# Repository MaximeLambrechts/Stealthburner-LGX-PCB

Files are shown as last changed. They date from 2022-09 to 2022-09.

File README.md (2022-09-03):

# PCB for Voron Stealthburner & Bondtech LGX

This mod is a custom 2-piece PCB design, as well as a few printed parts, to make the Bondtech LGX fully compatible with the Voron Stealthburner.

This mod is based on two existing mods, all credits go to them for the initial design :

* LGX Stealthburner Mount Remix by Symataris on Thingiverse ([link here](https://www.thingiverse.com/thing:5242645))
* Stealthburner toolhead PCB by Hartk1213 ([link here](https://github.com/hartk1213/MISC/tree/main/PCBs/Stealthburner_Toolhead_PCB))

I really like the 2-piece PCB design by Hartk, with which you just plug the stealthburner in the main board via a connector, without having to deal with cables from the fans and LEDs.

Instead of trying to source different parts from different mods and make them all compatible with each other, I decided to create this mod and design 2 new PCB's (one for the stealthburner, one on the LGX), as well as the printed parts required to have a fully completed Stealthburner + LGX, as cleanly assembled as possible.

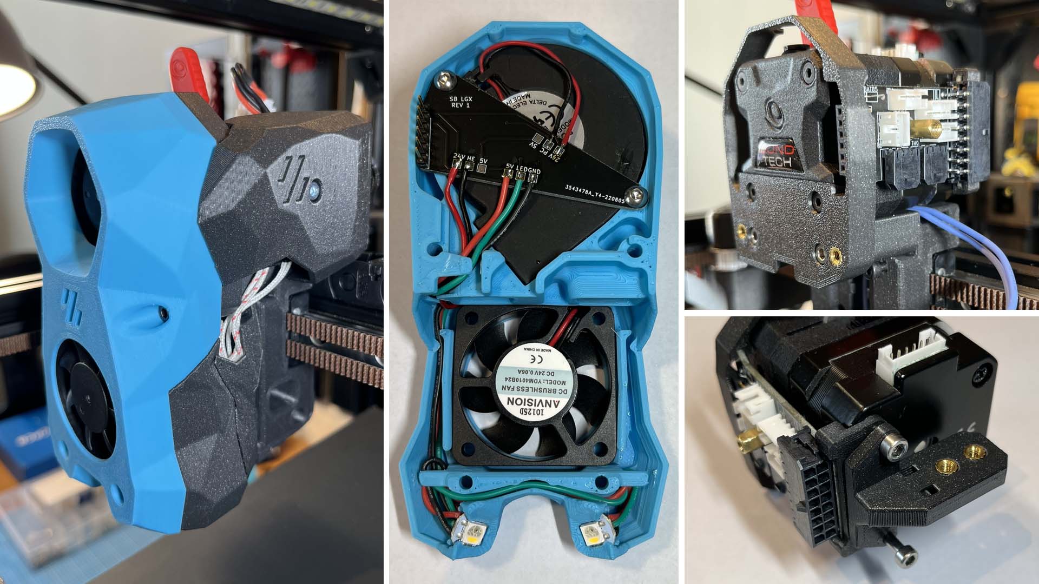
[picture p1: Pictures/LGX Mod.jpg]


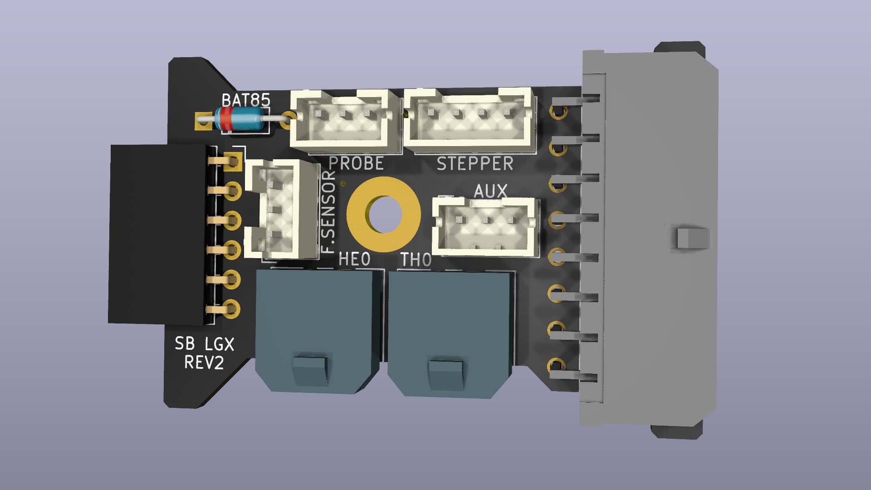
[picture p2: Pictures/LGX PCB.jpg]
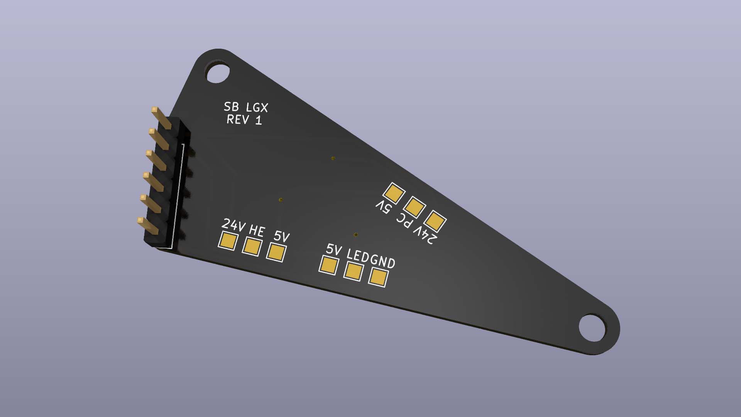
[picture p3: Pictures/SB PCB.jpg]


[1. Bill of Materials (BOM)](#1-bill-of-materials)

[2. Ordering PCBs](#2-ordering-pcbs)

[3. Printed parts](#3-printed-parts)

[4. Assembly Instructions](#4-assembly-instructions)

[5. Feedback](#5-feedback)

# 1. Bill of Materials (BOM)

Note: This BOM complements the original Stealthburner BOM. Only the extra compoments are included here. Items that are required for the original build are not included here. Refer to the stealthburner manual for a complete list of required components.

PCBs

* 1x Stealthburner side PCB (SB_PCB)
* 1x LGX side PCB (LGX_PCB)

Hardware

* 3x M3x6 Button head hex socket screws
* 1x 10mm standoff (female-female)
* 5x Heat set inserts (or 4 if using 2-hole cable chain)
* 1x M3x6 Socket head Cap Screws
* 2x M3x18 Socket head Cap Screws
* 2x M3x20 Socket head Cap Screws
* 2x M3x25 Socket head Cap Screws
* 2x M3x30 Socket head Cap Screws
* 2x M3x8 Flat head Screws (can be slightly longer, not critical)

Connectors & Electronics

* 1x Pin header, 6 pos, 2.54mm (Molex 22-28-4063)
* 1x Pin Socket, 6 pos, right angle through hole (Samtec SSW-106-02-G-S-RA)
* 1x Molex 43045-1600 (Board 16-pin receptacle)
* 1x Molex 43025-1600 (16-pin connector)
* 16x Molex 43030-0007 (contacts for wires)
* 2x Molex 43650-0200 (Hotend & Thermistor receptacles)
* 2x Molex 43645-0200 (Hotend & Thermistor connectors)
* 1x BAT85 diode (optional, if using probe only)
* 3x JST-PH 3-pin male & female
* 1x JST-PH 4-pin male & female

(Note: JST-PH connectors can be bought in assortment boxes on Amazon for example. I recommend this, as you would have multiple sizes in male/female in sufficient quantity for this and future projects, or should you need to recrimp a new cable for example)

Other

* 1x Small PTFE tube (2mm ID x 4mm OD) (length varies depending on your hotend. See assembly instructions).
* Small zipties

# 2. Ordering PCBs

Two Gerber zip files are provided for ordering the PCB's (**LGX_PCB_Gerber.zip** and **SB_PCB_Gerber.zip**).

I recommend JLCPCB or PCBWay for ordering the PCBs. I've personally ordered from JLCPCB and the boards were very cheap and worked perfectly.

An example order configuration for JLCPCB can be found [here](Pictures/PCB%20Order/JLCPCB.jpg).

An example order configuration for PCBWay can be found [here](Pictures/PCB%20Order/PCBWay.jpg).

Pay attention to the important settings (marked with an exclamation point) when ordering the PCB's!

The LGX PCB should be a **4-layer board of 1.6mm thickness**. (on JLCPCB only, you have to specify which layer is which, see picture)

The SB PCB should be a **2-layer board of 1.6mm thickness**.

Other parameters are personal preference, like the color of the board, or if you want lead-free HASL for example.

# 3. Printed parts

The following parts need to be (re)printed :

* **Stealthburner_Body.stl** (There are small differences to the original file. Some small cutouts for a better PCB fit and the PCB mounting
points have been modified.)
* **LGX_Mount.stl**
* **LGX_Rear_PCB_Support.stl**
* **Cover.stl**
* **Cable_Chain_Anchor_xHoles..stl** (Chose either the 2 or 3-hole version depending on your cable chain)

# 4. Assembly Instructions

Note: These instructions are a complement to the original Stealthburner assembly manual. Keep a copy of the original manual open in parallel 
to these instructions, as I will often refer to it.

## Preparing the PCBs

* Solder the components on the LGX pcb as shown on the picture. Make sure the 6-pin socket lays nice and flat on the PCB and is soldered straight. This is important for correct connection with the stealthburner later on.

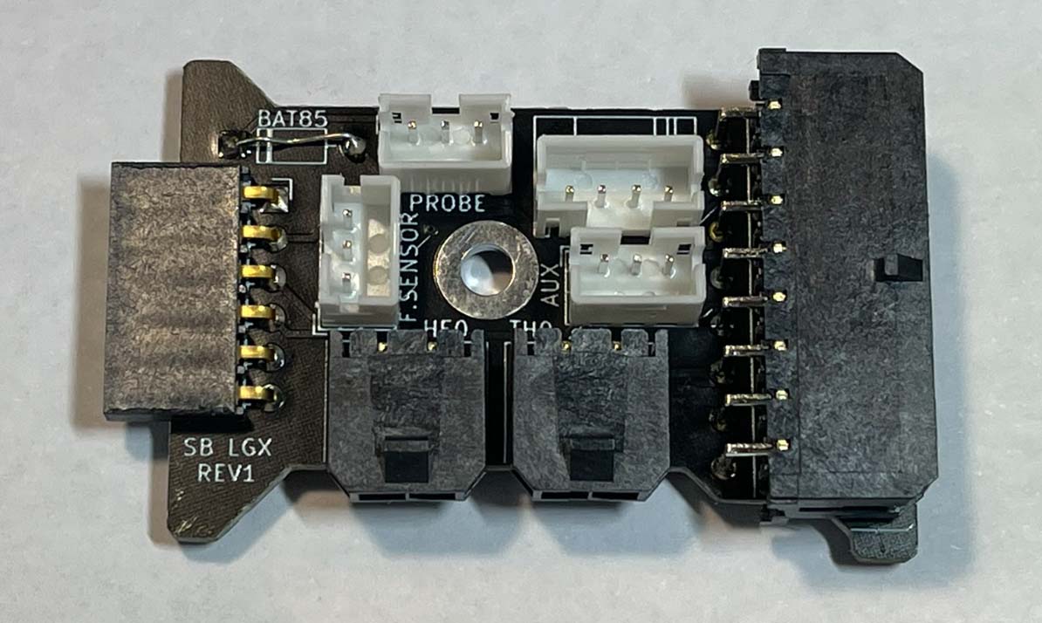
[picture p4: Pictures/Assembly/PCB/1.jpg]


* If you're not using an inductive probe (for example Klicky or KlickyNG mod with microswitch), replace the BAT85 diode by a small piece
of wire to short the pads. A leg from a donor component (LED or resistor for example) works well here.

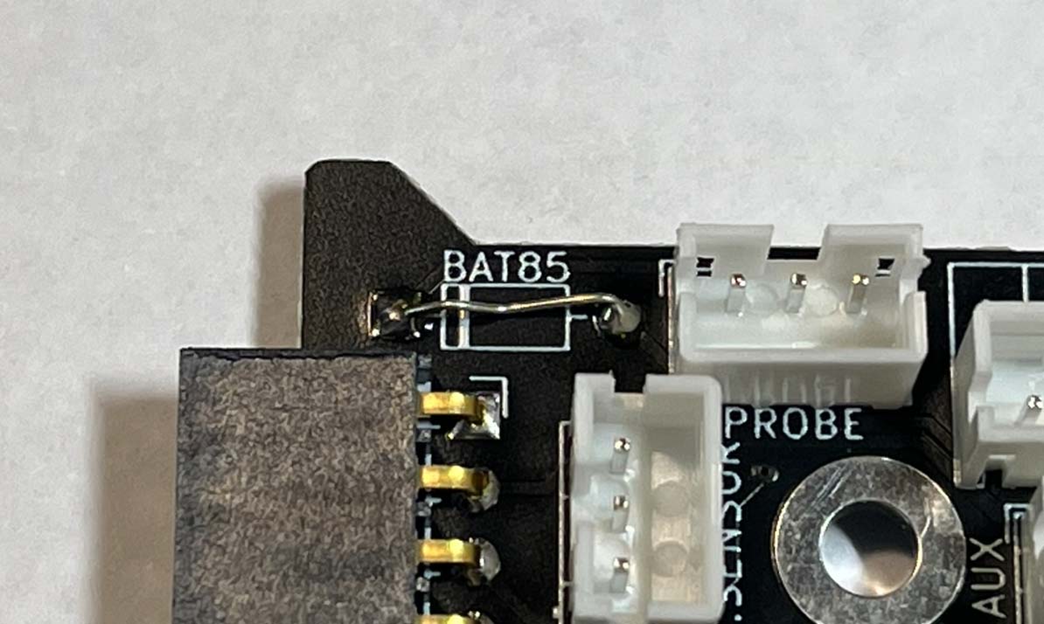
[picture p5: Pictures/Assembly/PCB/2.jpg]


* Install a 10mm standoff using an M3x6 button head screw.
Make sure the screw head **does not stick out more than 2mm from the PCB**.
Make sure **no solder points stick out more than 2mm**. (to avoid touching and potentially shorting on the LGX extruder motor later on)

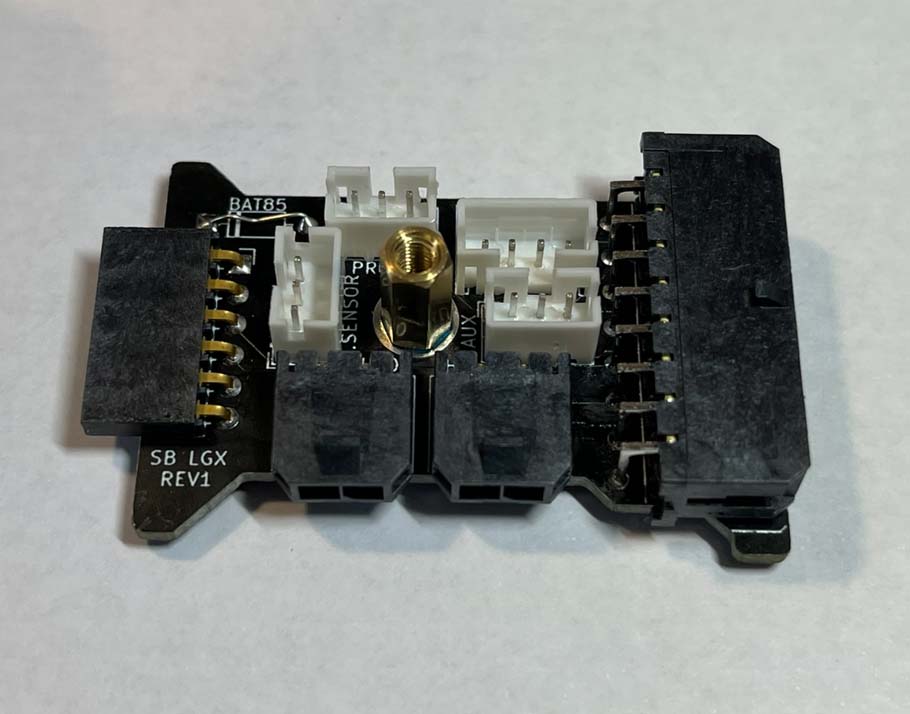
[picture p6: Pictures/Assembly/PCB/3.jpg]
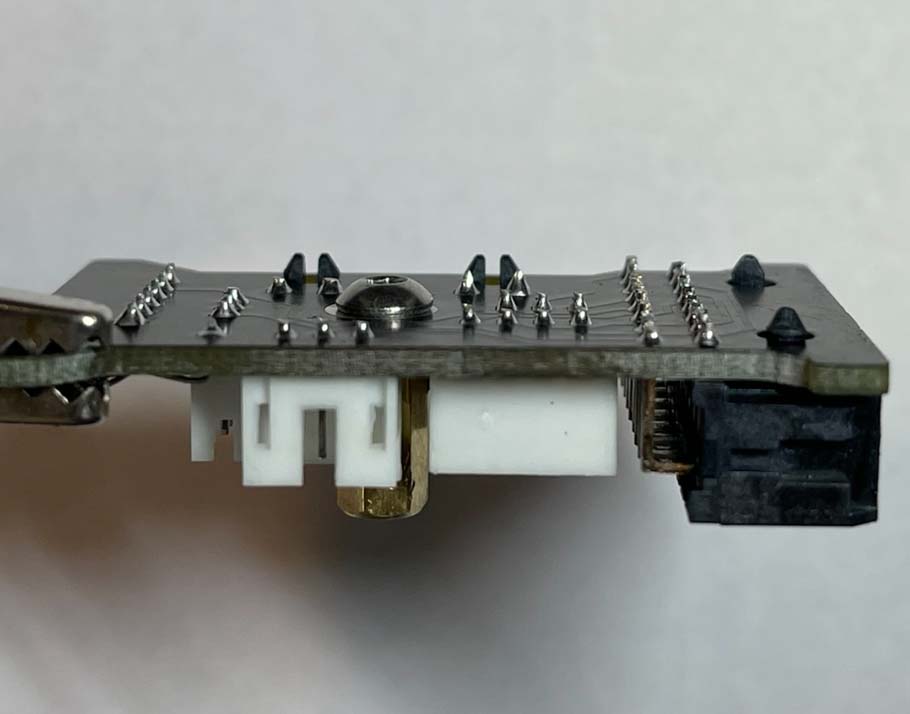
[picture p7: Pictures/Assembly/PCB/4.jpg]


* Solder a 6-pin header to the SB PCB. The pins should face up.

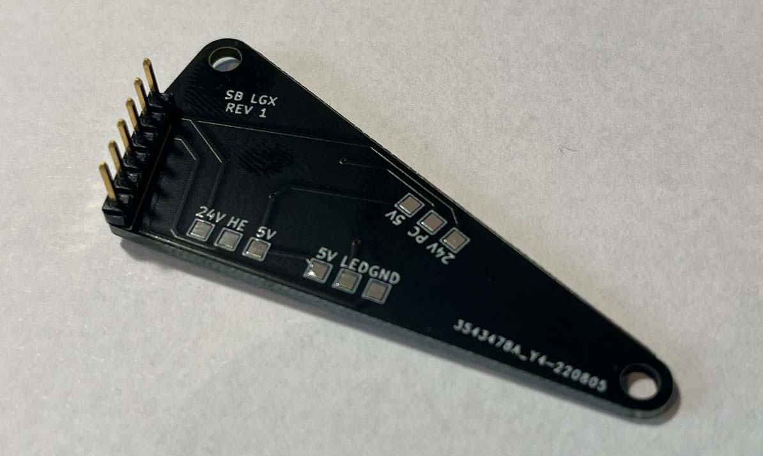
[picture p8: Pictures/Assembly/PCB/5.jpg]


## Stealthburner

* Follow the original manual instructions to install the LED's and fans into the stealthburner body. Leave the cables hanging for now.

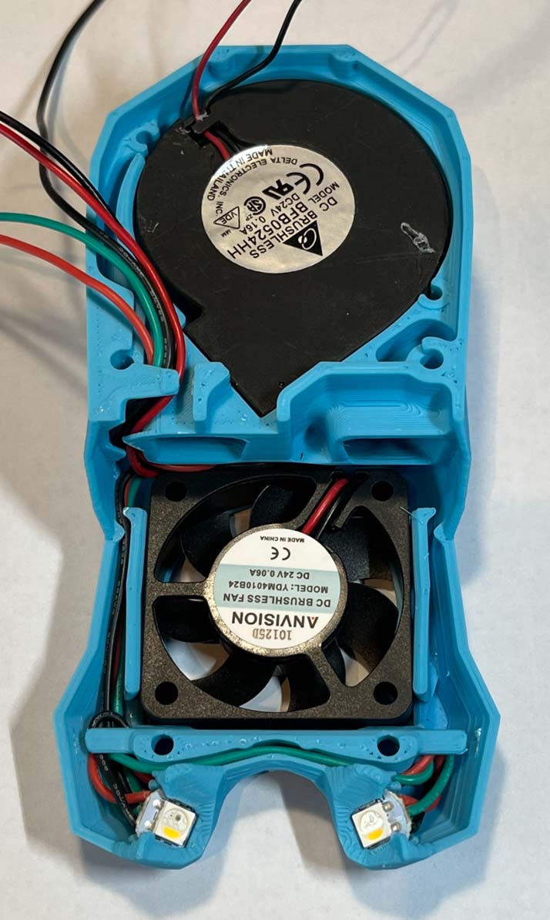
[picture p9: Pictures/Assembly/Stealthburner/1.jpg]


* Install the PCB into the SB body and fasten with 2 M3x6 button head screws.
**Warning**: Do not overtighten as these screw into plastic.

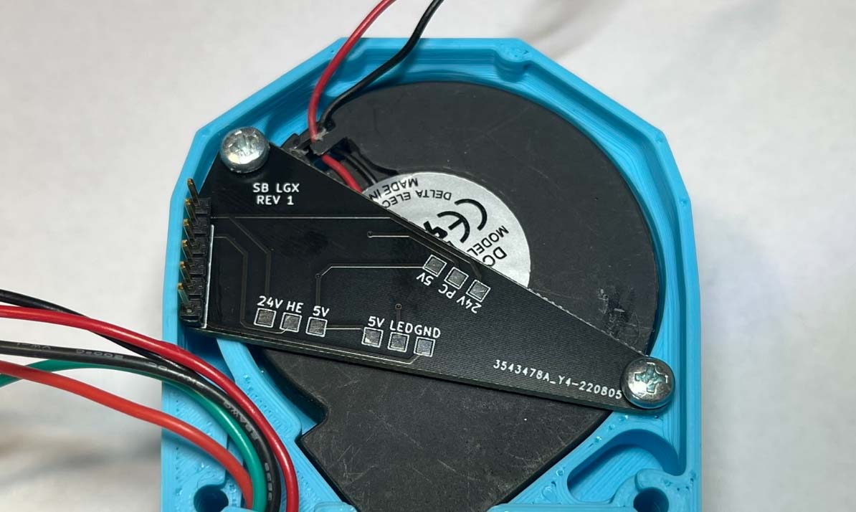
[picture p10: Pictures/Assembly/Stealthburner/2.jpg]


* Make sure the screws do not stick out of the SB body, or there would be a clearance issue with the LGX. (That's the reason why button head screws are used here instead of socket head)

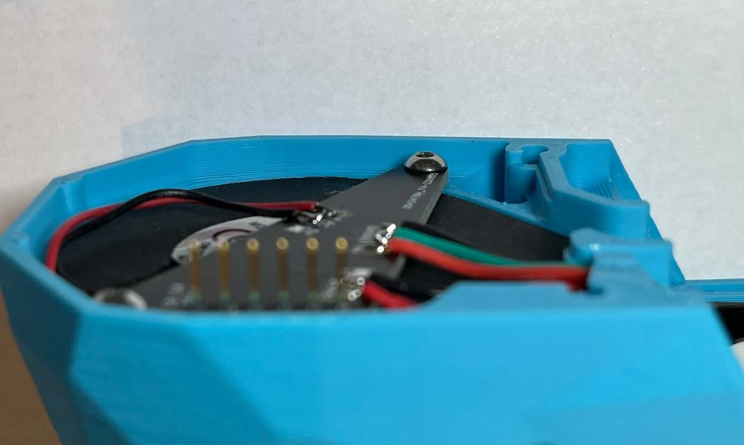
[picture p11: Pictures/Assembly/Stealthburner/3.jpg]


* Solder all the wires onto the PCB as shown on the picture below. Note: The red (positive) wire of both fans can be soldered to either 24V or 5V 
depending on the voltage of your fans.

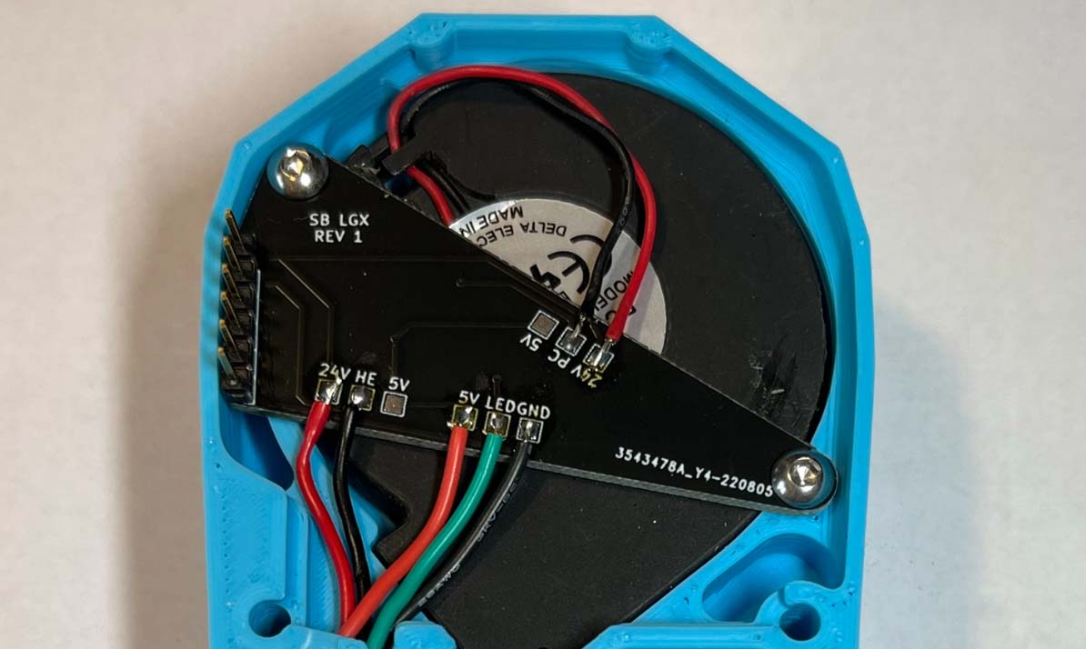
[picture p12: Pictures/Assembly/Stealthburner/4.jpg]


## Printhead

* Follow the stealthburner manual to assemble the printhead. You can print either the CW1 or CW2 version of the printed parts.

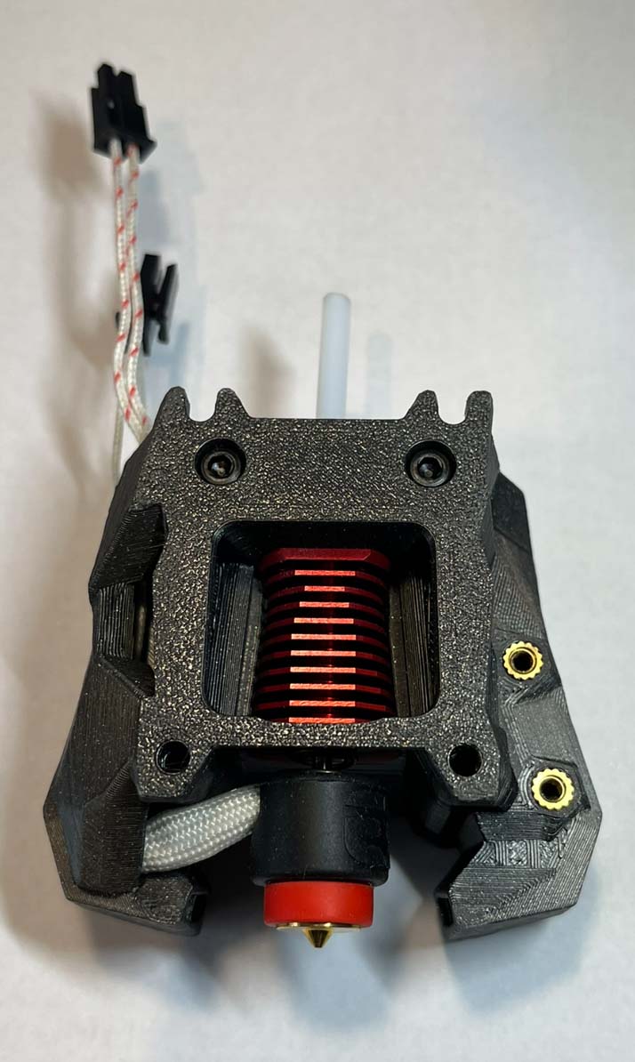
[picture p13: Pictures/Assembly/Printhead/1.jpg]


* Install the PTFE tube into the hotend. The length of the tube will vary depending on your hotend. The tube should stick out **25mm** from the top of the printed part.

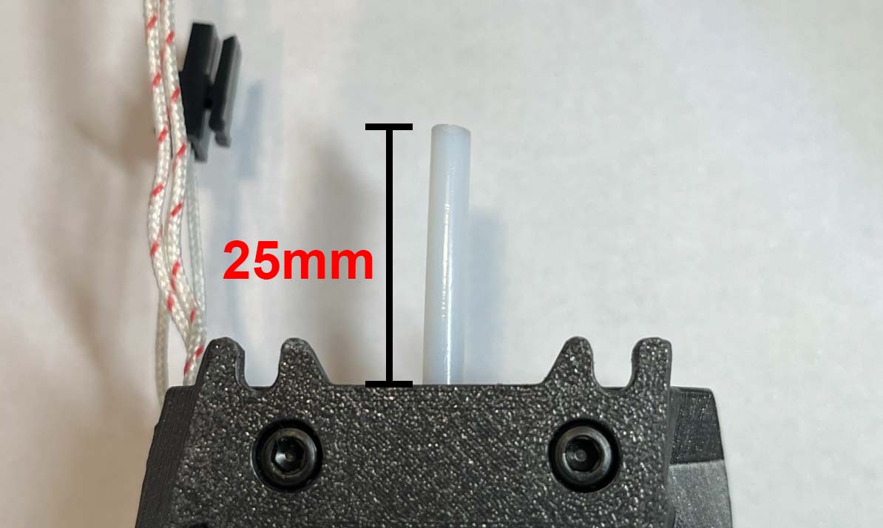
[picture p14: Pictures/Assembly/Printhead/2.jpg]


## LGX

* Install 2 heat set inserts into the LGX Mount as shown. 
Install 2 (or 3) heat set inserts into the cable chain anchor as shown.

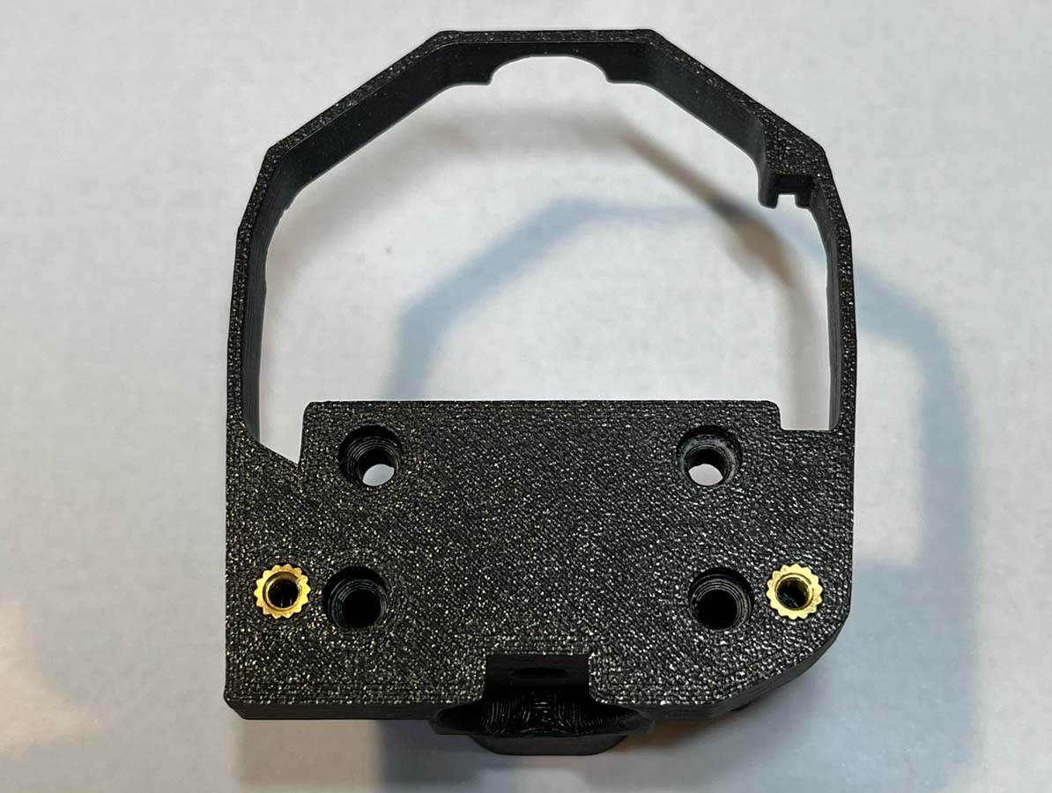
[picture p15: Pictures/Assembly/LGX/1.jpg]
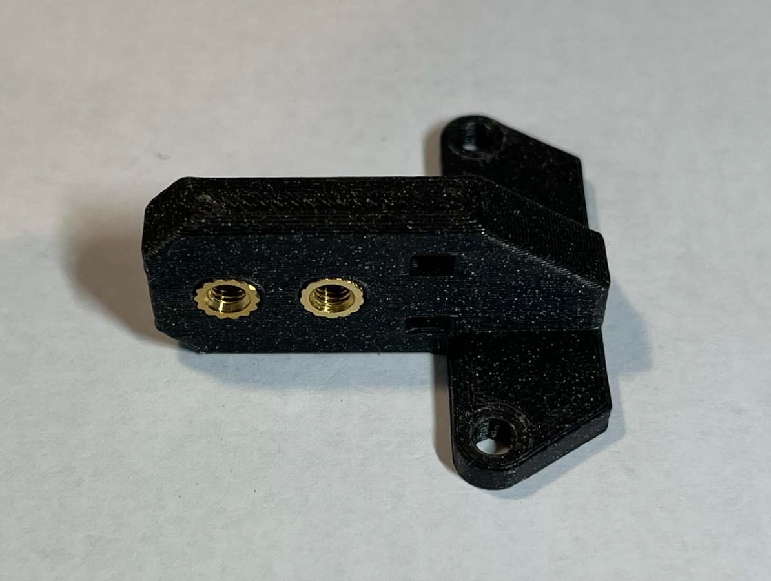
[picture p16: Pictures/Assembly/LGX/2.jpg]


* dissasemble the front part of your LGX extruder.

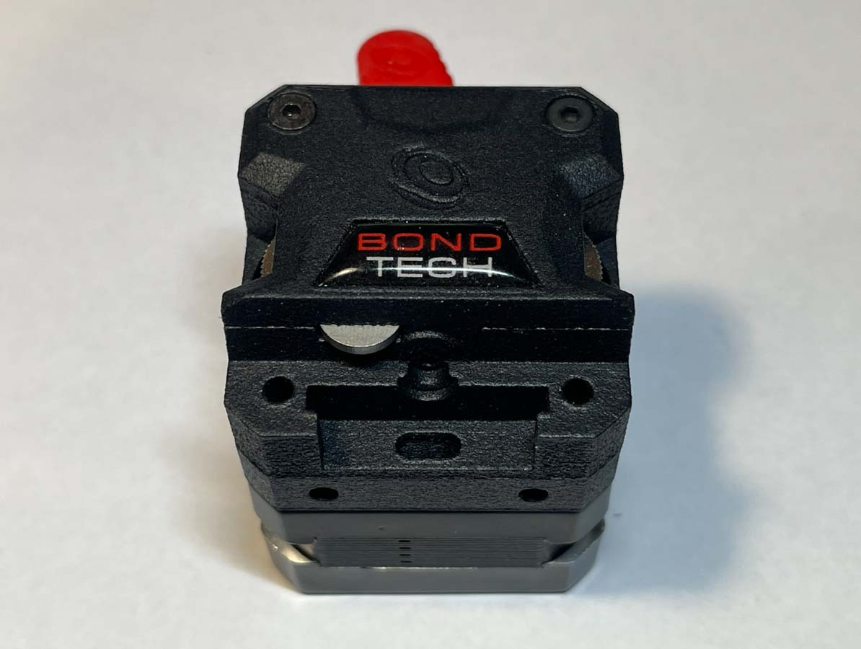
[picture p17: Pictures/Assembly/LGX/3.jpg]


* On the backside, remove the 2 left screws.

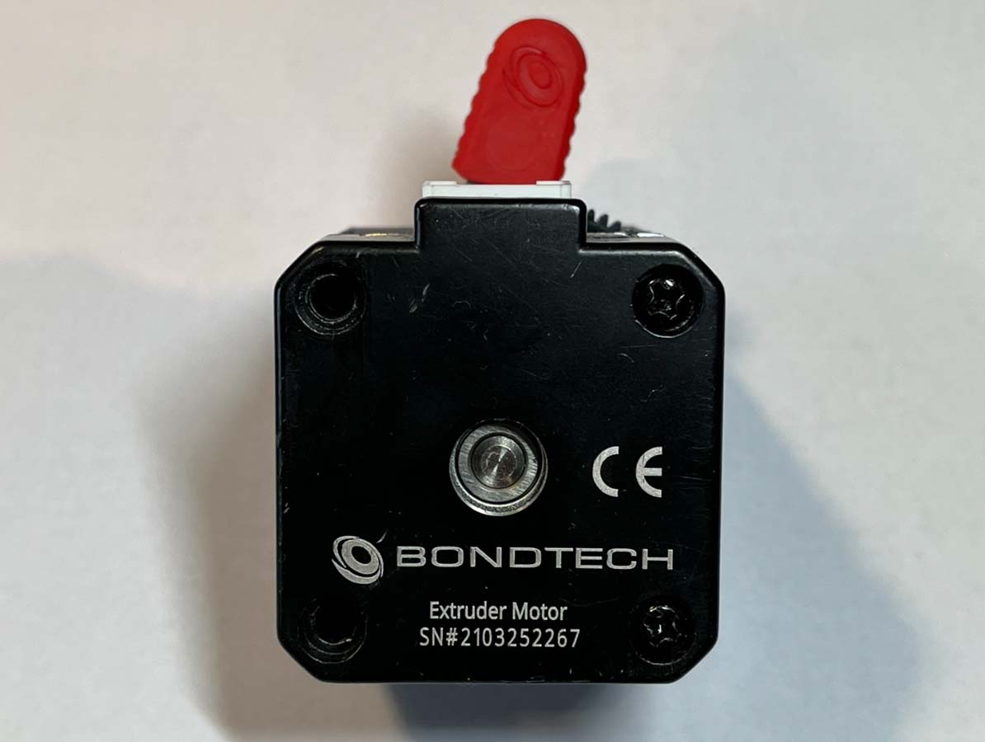
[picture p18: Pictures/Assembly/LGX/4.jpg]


* Slide the LGX_Mount onto the LGX extruder and fasten with 2 M3x20 on the bottom and two M3x27 (original screws from LGX) on the front.

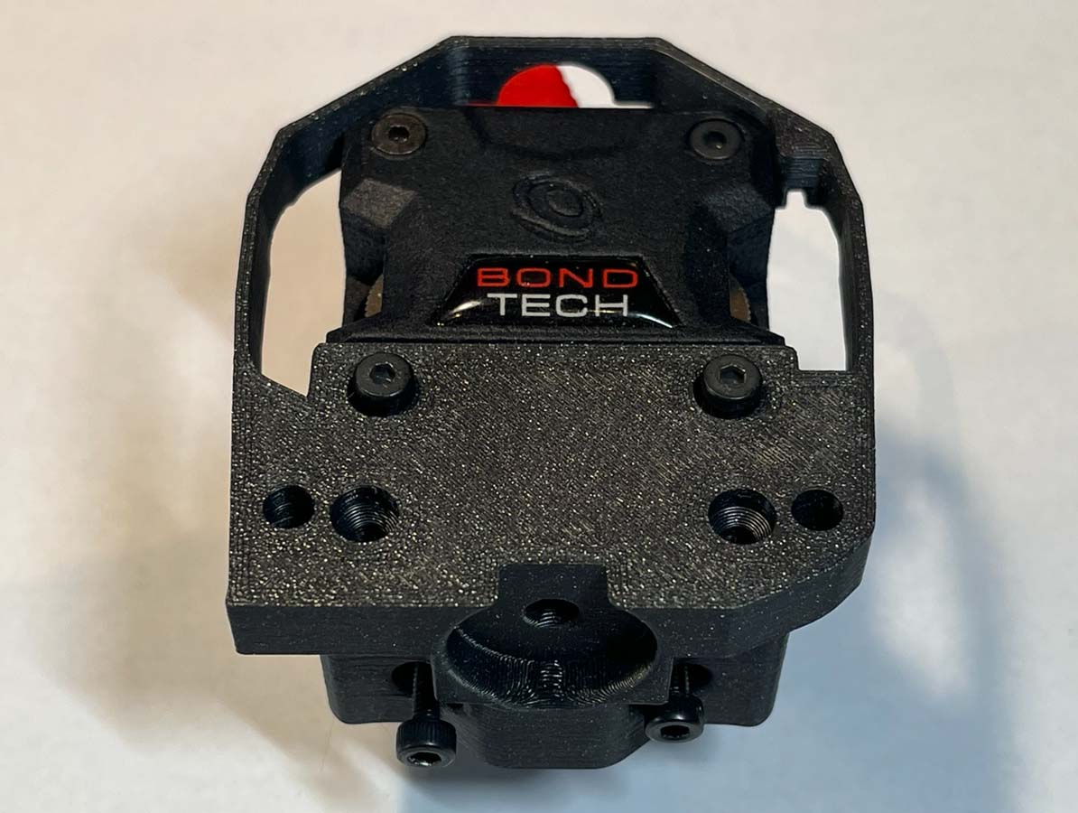
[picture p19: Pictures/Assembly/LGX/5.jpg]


* Slide the PCB into the LGX_Mount printed parts grooves until it is fully seated into place.

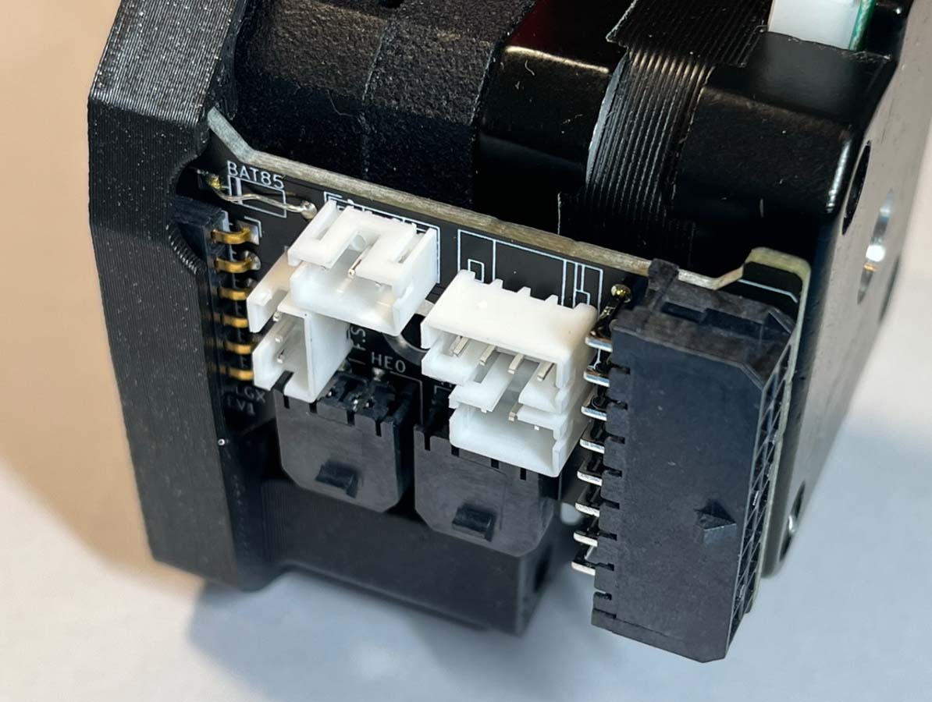
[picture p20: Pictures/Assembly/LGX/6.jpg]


* Install the PCB rear support printed part. It should slide onto the PCB and insert into the holes of the extruder motor.

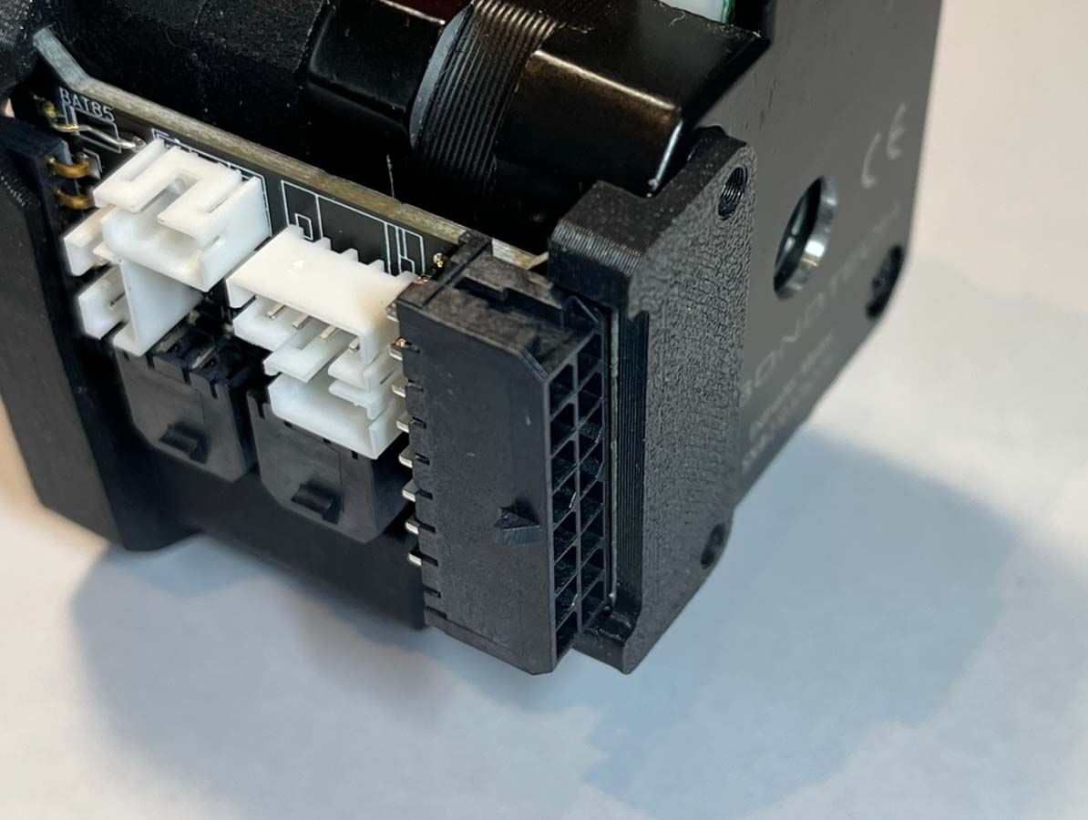
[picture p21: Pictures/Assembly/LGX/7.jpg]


* Install the cable chain anchor and fasten everything together with 2 M3x25 screws.

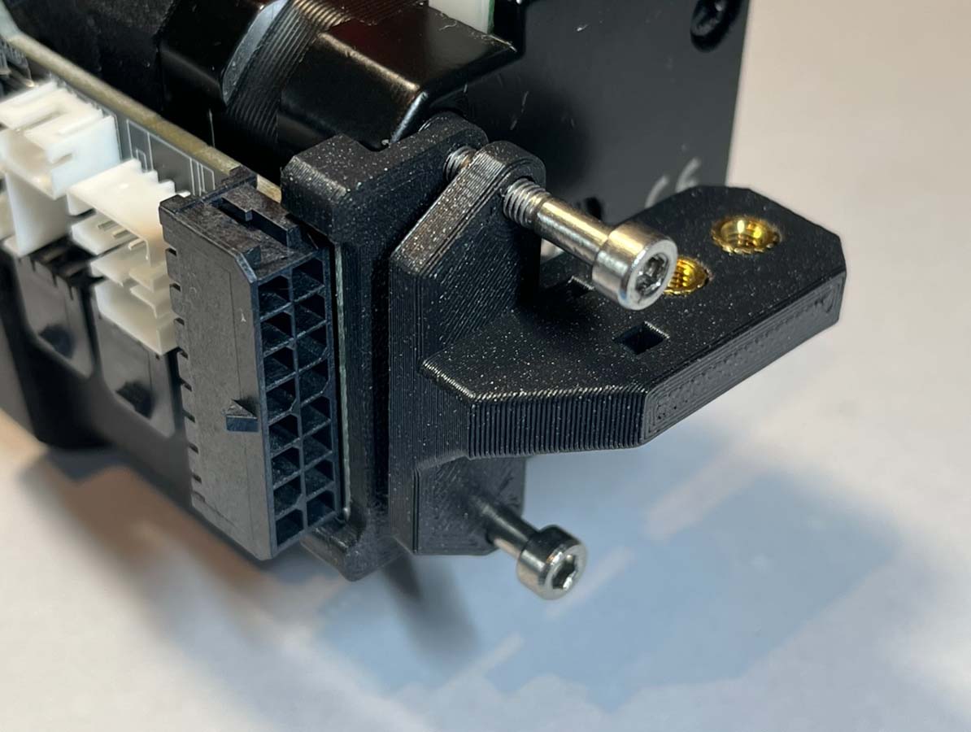
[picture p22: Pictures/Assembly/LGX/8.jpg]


* Now is a good time to make sure no solder points touch the LGX extruder motor.

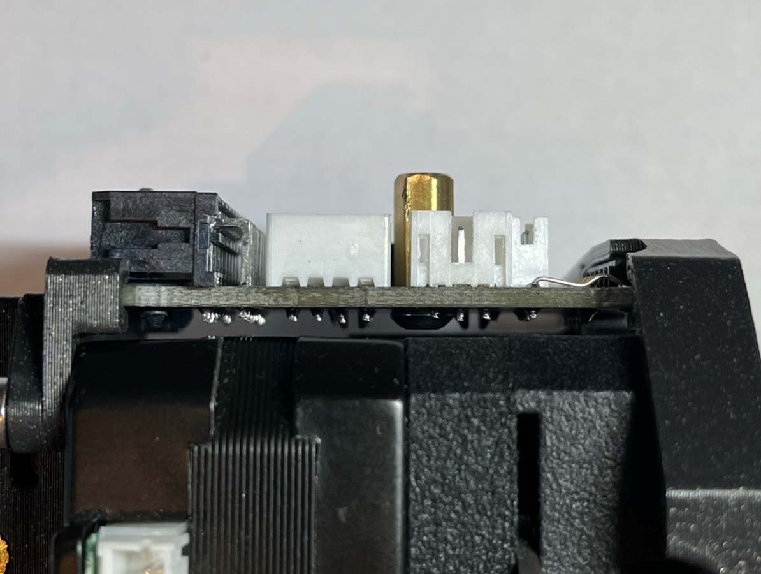
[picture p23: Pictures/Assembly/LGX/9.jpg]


## Final Assembly

* Follow the stealthburner manual to install the carriage and probe (or klicky).

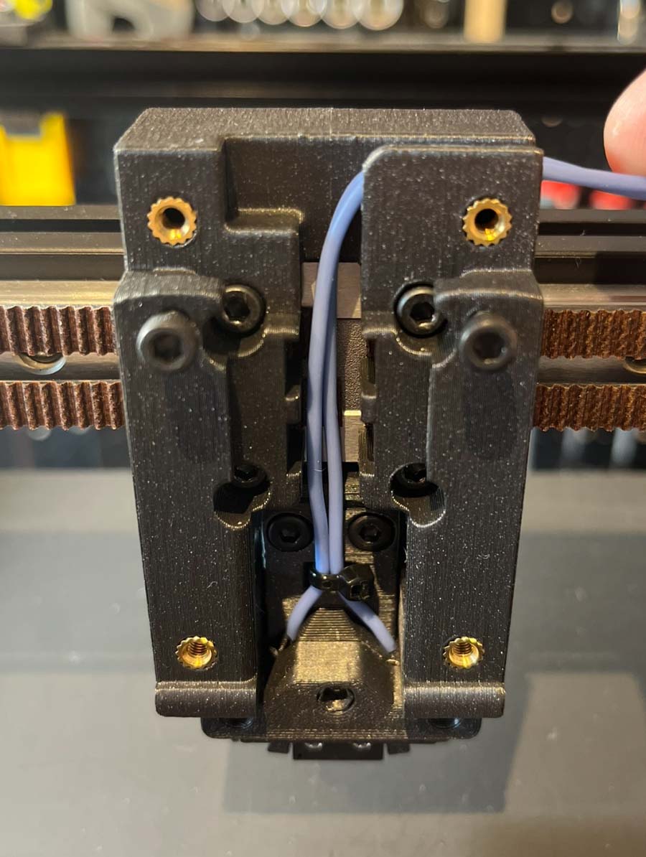
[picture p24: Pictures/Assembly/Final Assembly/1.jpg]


* Fasten the LGX assembly onto the carriage with 2 M3x30 screws.
Make sure the probe wires are routed correctly and are not pinched between the carriage and LGX.

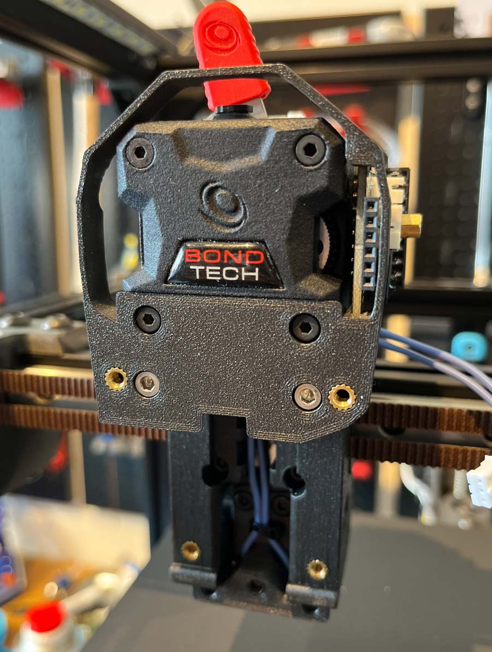
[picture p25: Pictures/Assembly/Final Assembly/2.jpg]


* Slide the printhead from the bottom into the LGX assembly. Make sure it is fully inserted, flush with the LGX mount, and flush on the X-carriage.

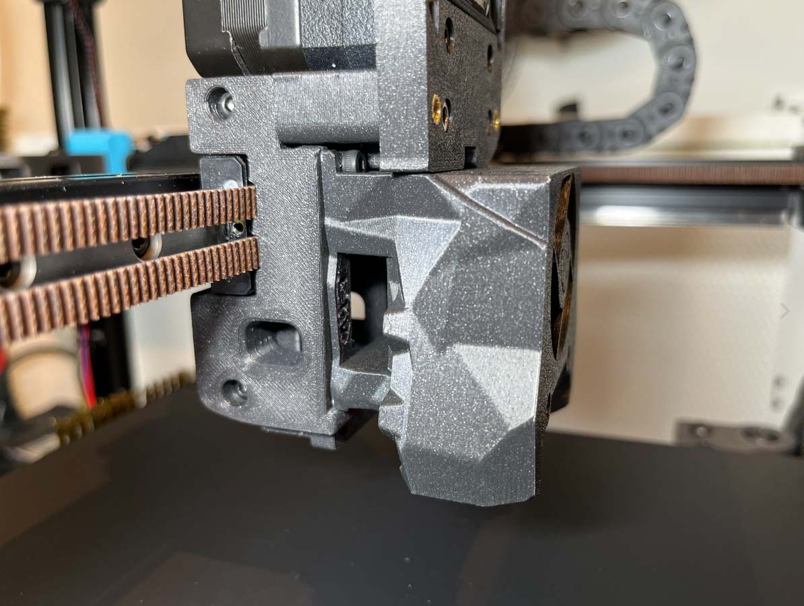
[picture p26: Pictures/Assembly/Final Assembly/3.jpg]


* Slide the Stealthburner in place. Make sure the pins align correctly with the socket. It is recommended to first align and insert the pins, then slide the SB fully in place.

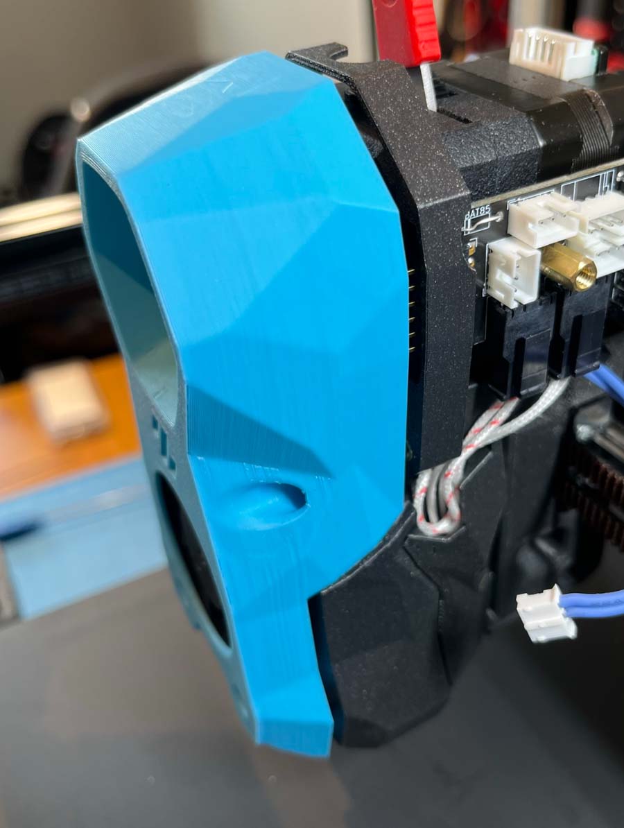
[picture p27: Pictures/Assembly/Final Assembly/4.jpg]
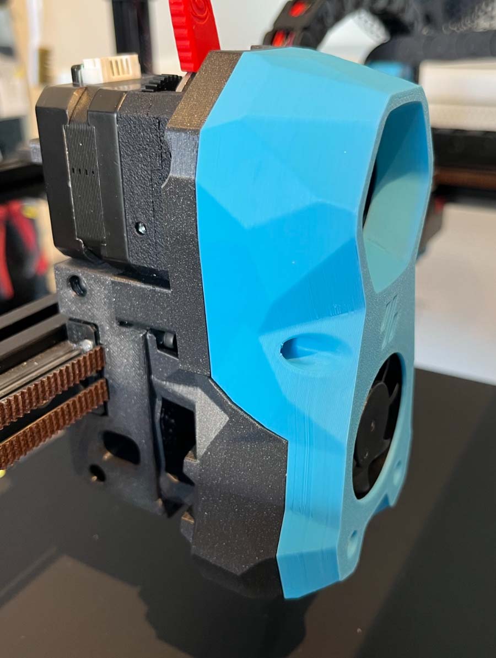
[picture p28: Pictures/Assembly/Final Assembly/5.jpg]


* Fasten the Stealthburner with 2 **M3x18** screws on top, and 2 **M3x50** screws on the bottom.

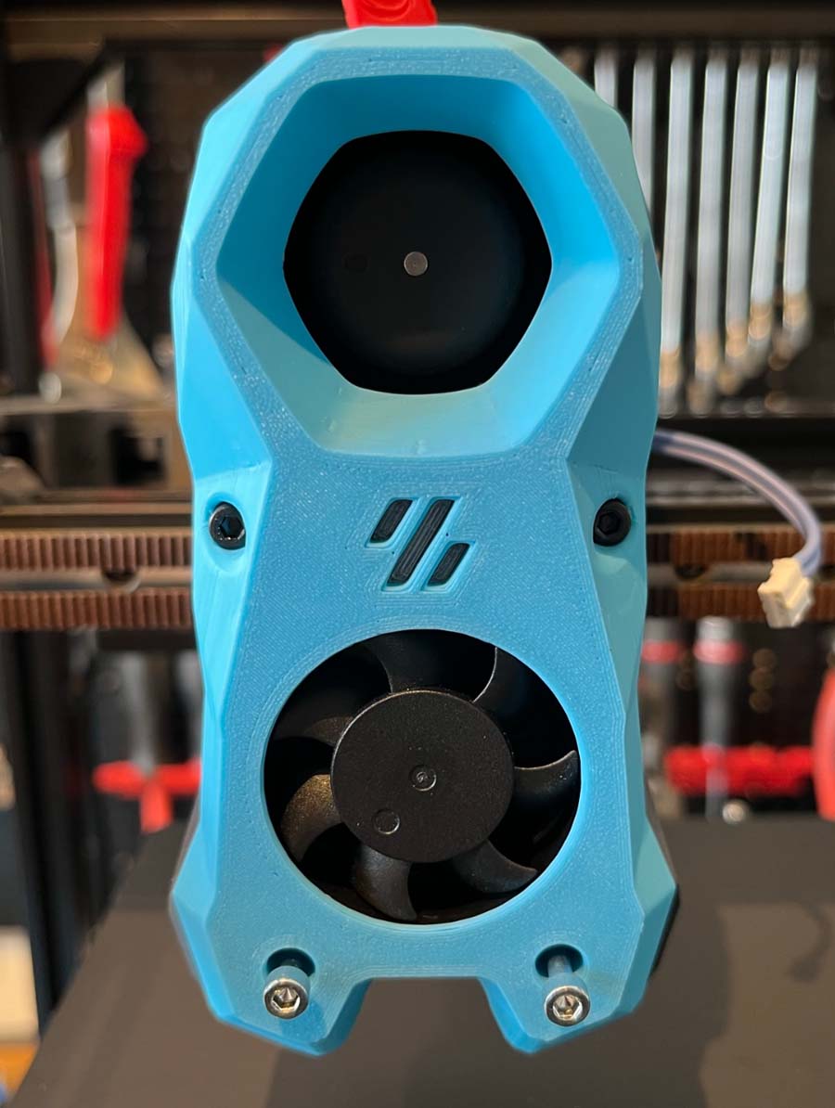
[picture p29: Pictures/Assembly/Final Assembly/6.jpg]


* Prepare a small cable for the extruder motor with JST-PH connectors as shown. Its length should be about **90mm**.

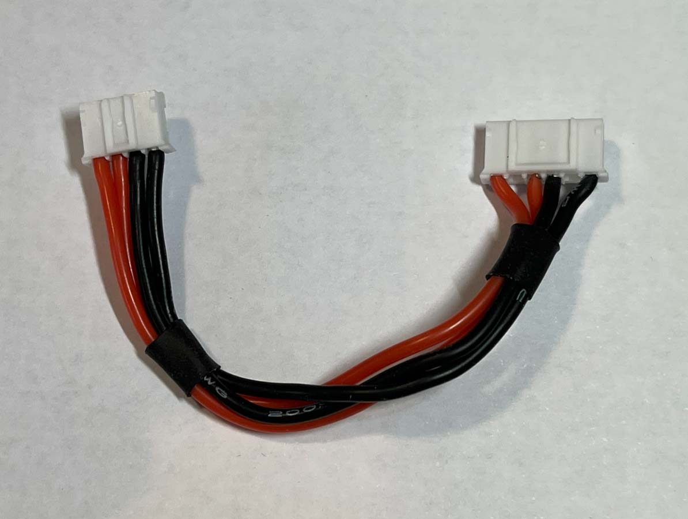
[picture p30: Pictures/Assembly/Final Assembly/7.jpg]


* Install the extruder motor cable.

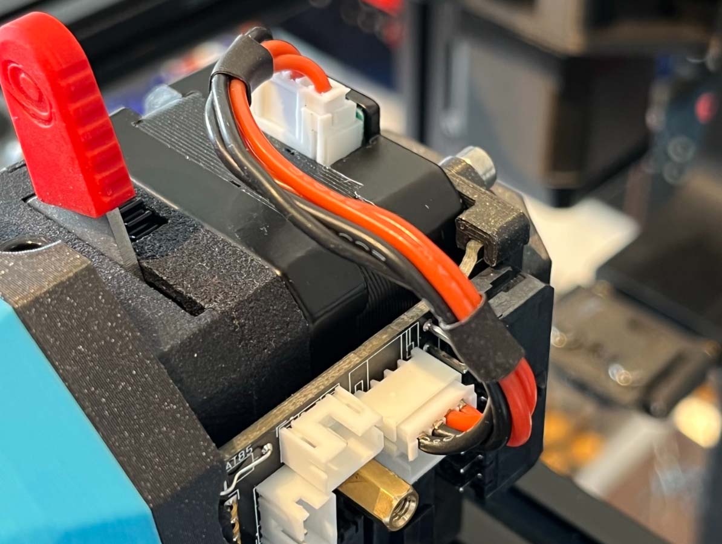
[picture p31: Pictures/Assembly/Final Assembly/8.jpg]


* Wire up the rest of the components, including the hotend, thermistor, probe or switch, etc

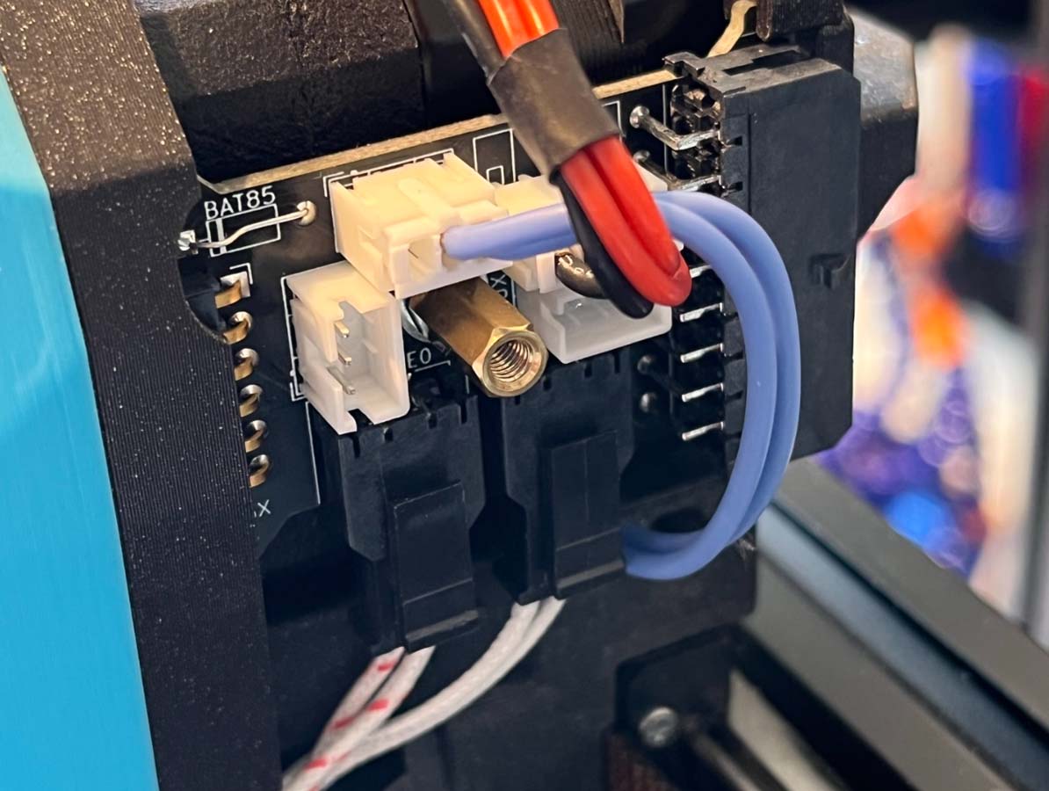
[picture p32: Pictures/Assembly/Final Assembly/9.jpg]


* Fasten the cable chain with 2 M3x8 flat head screws.
Install a ziptie into the ziptie slot.

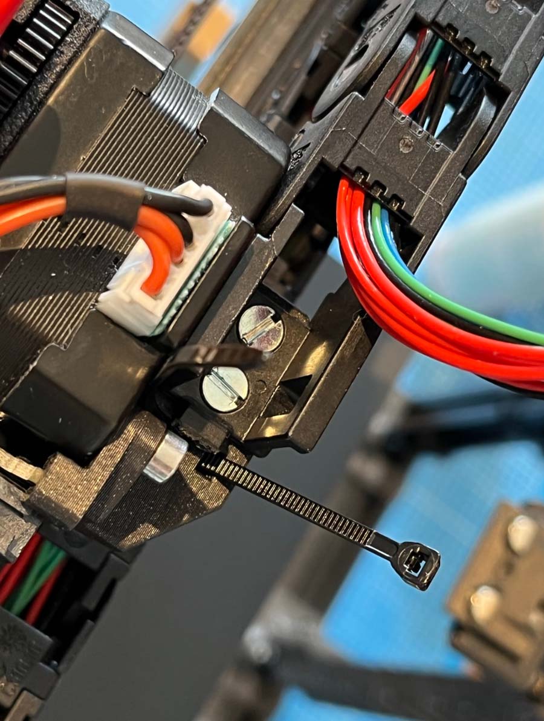
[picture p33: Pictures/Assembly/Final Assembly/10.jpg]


* Wire up and install the 16-pin connector. The wiring schematic is the same as the original Hartk PCB. The only difference is that the 14 and 2-pin connectors have been joined into a single 16-pin connector. The individual wires position is identical. See the wiring instructions [here](https://github.com/hartk1213/MISC/tree/main/PCBs/Stealthburner_Toolhead_PCB/Images/Wiring).

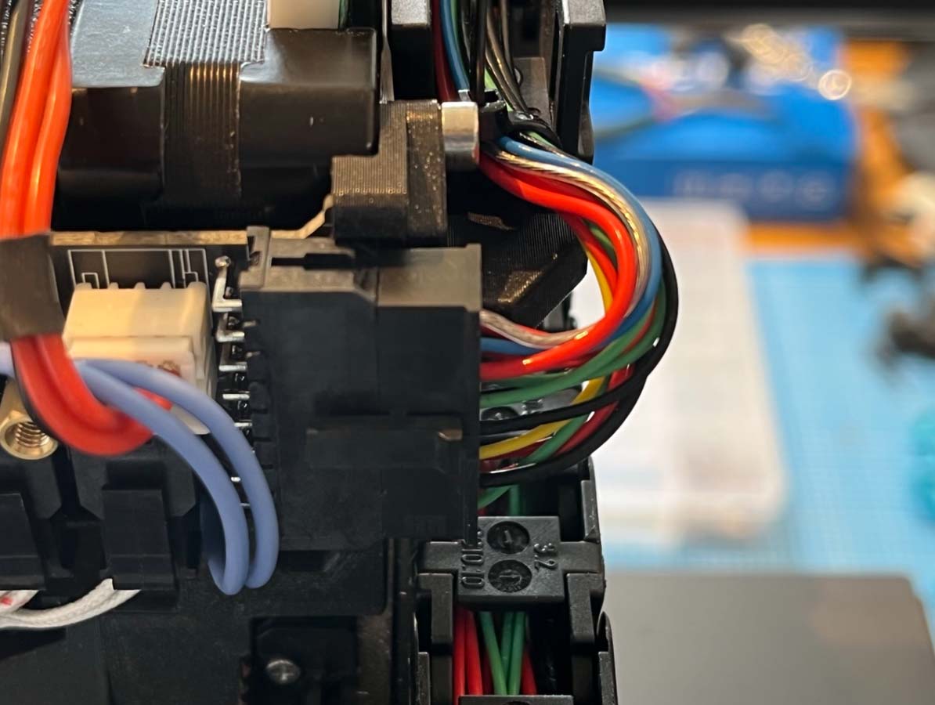
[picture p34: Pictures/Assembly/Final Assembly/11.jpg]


* Optionally, install a chamber thermistor. I've attached mine at the backside on the cable chain and routed the wires to the AUX connector on the PCB.

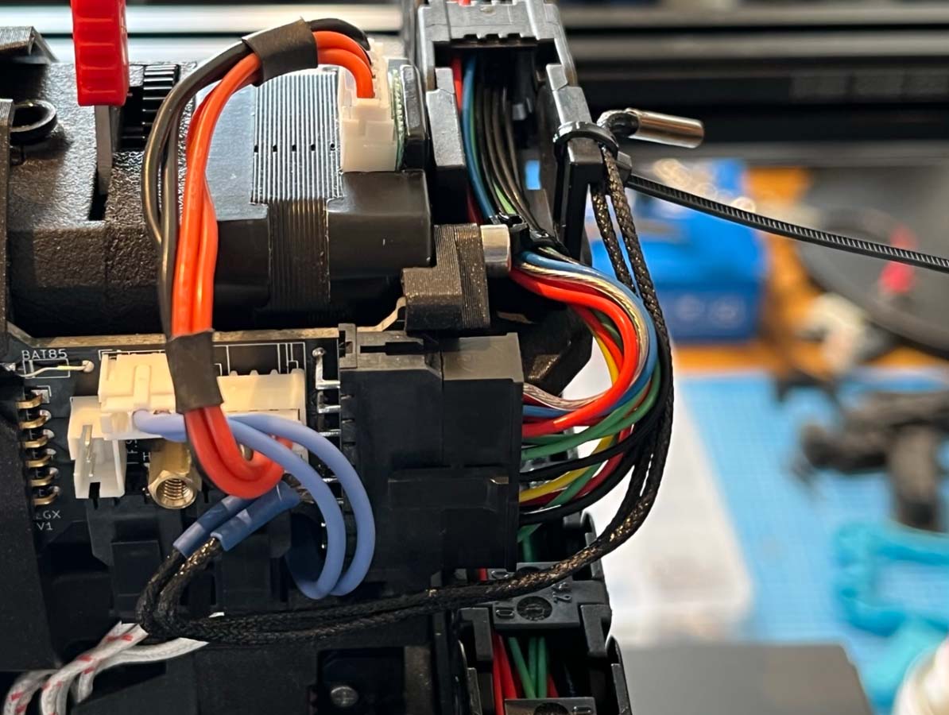
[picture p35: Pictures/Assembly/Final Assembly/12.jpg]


* Install the cover by sliding the backside over the M3 screws sticking out of the LGX, and then fasten on the side with 1 **M3x6** Socket head Screw.

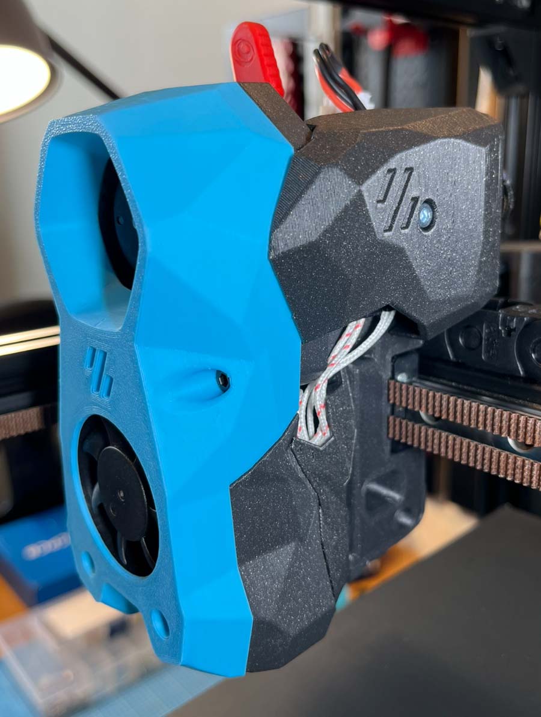
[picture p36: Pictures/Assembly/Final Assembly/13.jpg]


## Done ! Happy printing!

# 5. Feedback

While I've manage to assemble everything on my printer, there may be issues I haven't thought of, mistakes on this page, or issues that will only arise after many hours of printing.

**USE THIS MOD AT YOUR OWN RISK!**

I'd appreciate any kind of feedback, good or bad.

If you encounter issues, please open an issue on this github page.

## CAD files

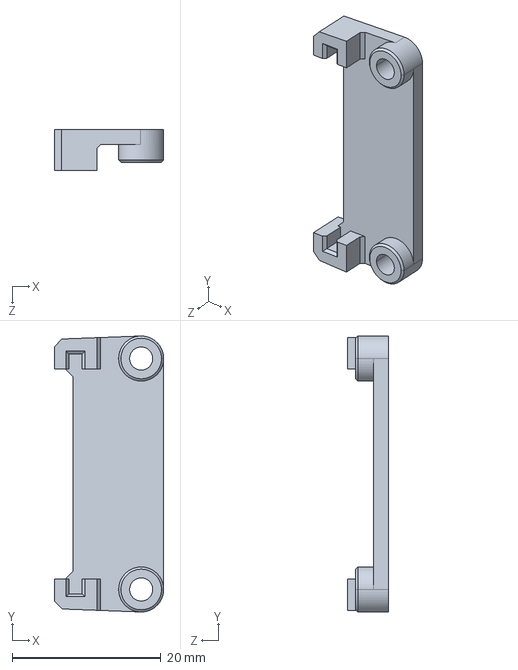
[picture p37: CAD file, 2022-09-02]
CAD/LGX_Rear_PCB_Support.STEP
14.7 x 37.1 x 5.50 mm

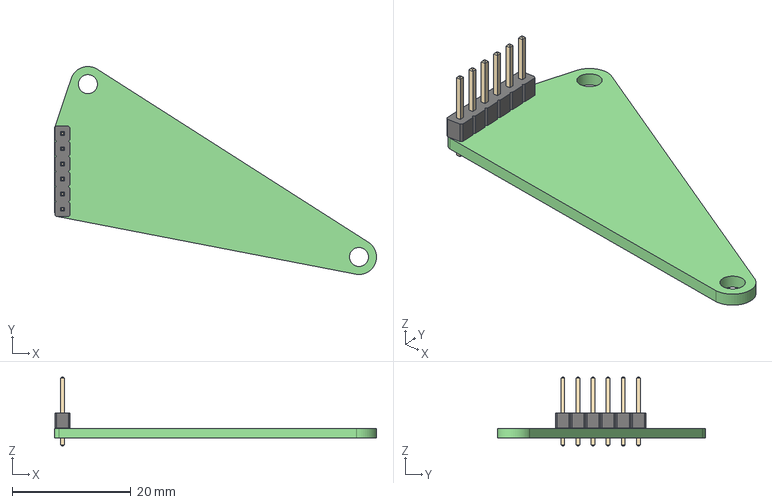
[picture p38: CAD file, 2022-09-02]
CAD/PCB/SB_PCB.step
54.1 x 35.0 x 11.5 mm
SB_PCB PCB

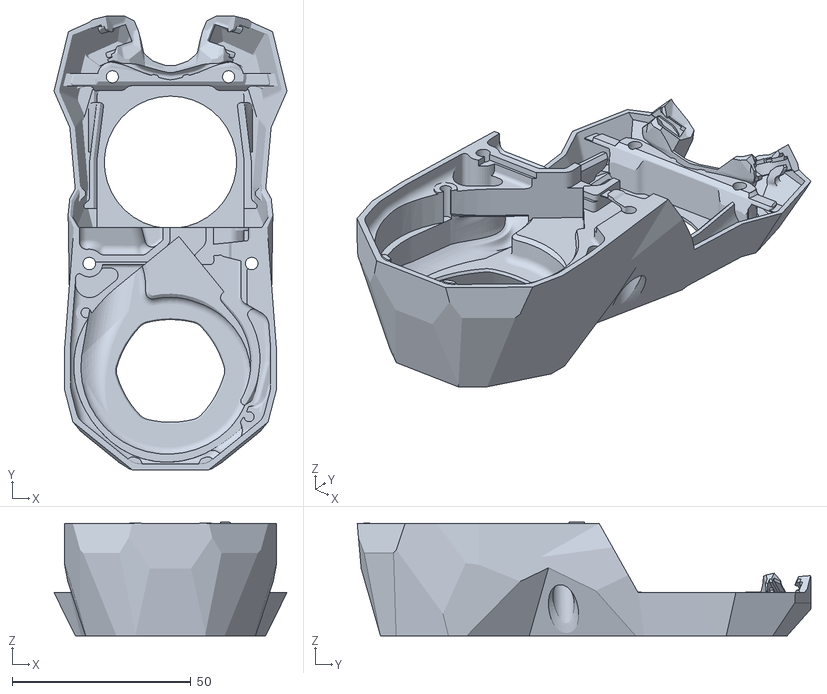
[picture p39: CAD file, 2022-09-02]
STL/Stealthburner_Body.STL
65.1 x 126.8 x 31.8

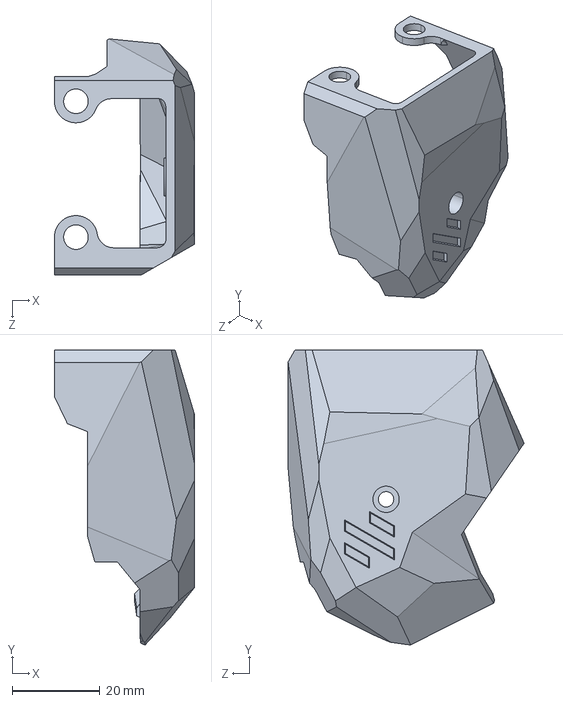
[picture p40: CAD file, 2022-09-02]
CAD/Cover.STEP
32.0 x 67.3 x 53.9 mm

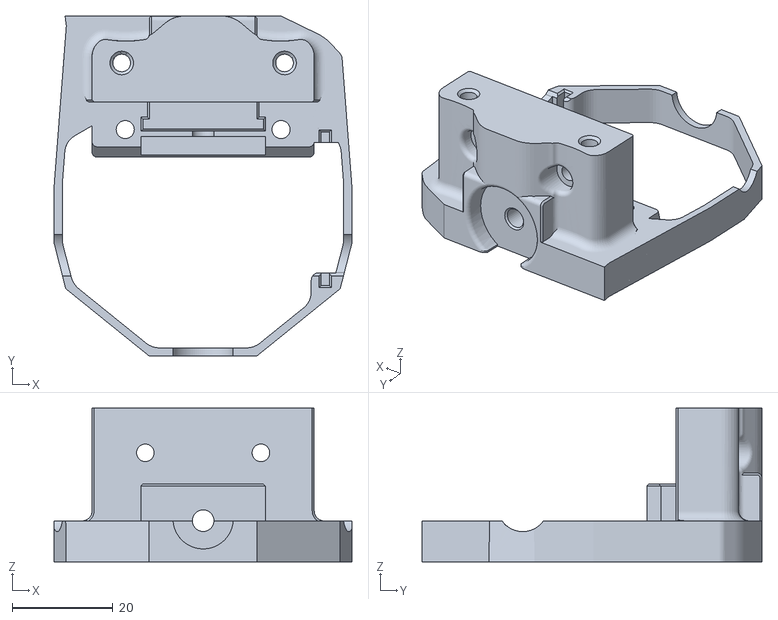
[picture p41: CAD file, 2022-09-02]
STL/LGX_Mount.STL
59.2 x 67.6 x 30.6

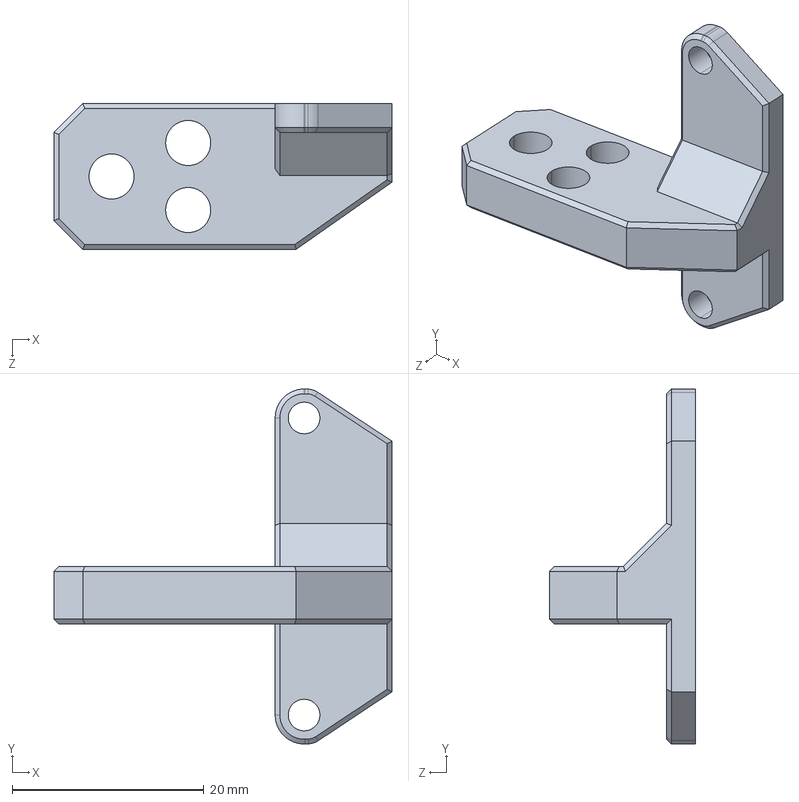
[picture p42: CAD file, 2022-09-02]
CAD/Cable_Chain_Anchor_3Holes.STEP
35.3 x 37.0 x 15.2 mm

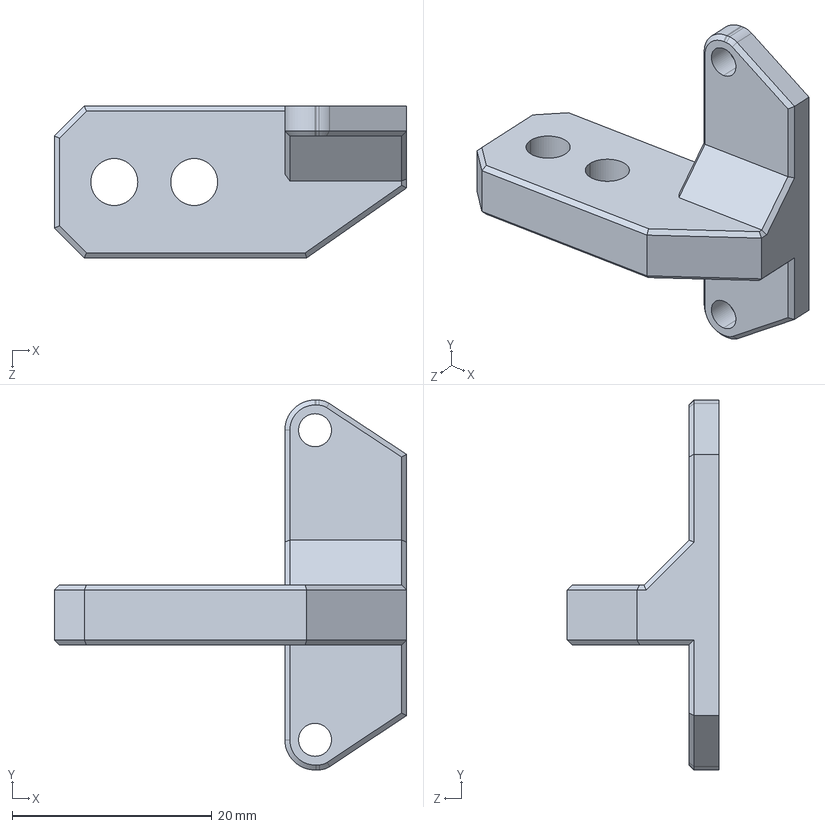
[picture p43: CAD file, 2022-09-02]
CAD/Cable_Chain_Anchor_2Holes.STEP
35.3 x 37.0 x 15.2 mm

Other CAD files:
STL/Cable_Chain_Anchor_2Holes.STL
STL/Cable_Chain_Anchor_3Holes.STL
STL/Cover.STL
STL/LGX_Rear_PCB_Support.STL

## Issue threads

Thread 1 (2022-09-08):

[Request] Incorporate the ERCF toolhead sensor port into the LGX mount.

devsfan1830, 2022-09-08:
Basically wonder if you would be able to make a version of your LGX mount based on the modification from this mount (https://github.com/EtteGit/EnragedRabbitProject/blob/main/usermods/LGX_Toolhead_Sensor/STL/LGX%20Front%20Mount.stl) to allow for the ERCF sensor to fit as well. If so this would be PERFECT for my intended eventual setup. As it stands now, I have the ERCF board and LGX based setup from the afterburner toolhead. But I intend to switch to stealth burner. Your mod as far as I know is the CLEANEST setup yet for a normal LGX based extruder. Even if I did go LGX lite, there doesn't appear to be ERCF support yet for that.

MaximeLambrechts, 2022-09-09:
Hi !

I'll look into it. But I think it is very doable yes :) My PCB has the filament sensor connector and pinout exactly as on the original pcb from Hartk, so that's a good thing already.

devsfan1830, 2022-09-10:
I dunno if its gonna work actually. I just made a rather crude brute force attempt to copy the cutout for the sensor into your mount model. It looks like the switch used for the ERCF sensor collides with the path of a screw used to mount to the LGX. Maybe that screw can be left unattached? I dont have an assembly to test myself.

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

devsfan1830, 2022-09-10:
Actually, I think I used the wrong LGX mount for ERCF. I pulled that file from usermods. There appears to be a new standard mount using a different sensor setup: https://github.com/EtteGit/EnragedRabbitProject/blob/main/Filament_Sensor/Stls/LGX/LGX_on_AfterBurner_Adapter_ERCF_Sensor.stl

Ive also now just learned ERCF no longer uses a toolhead sensor? So maybe this is no longer necessary?

devsfan1830, 2022-10-03:
Yeah ERCF has gone sensorless on the toolhead so no need to do this anymore.

Closed 2022-10-03.

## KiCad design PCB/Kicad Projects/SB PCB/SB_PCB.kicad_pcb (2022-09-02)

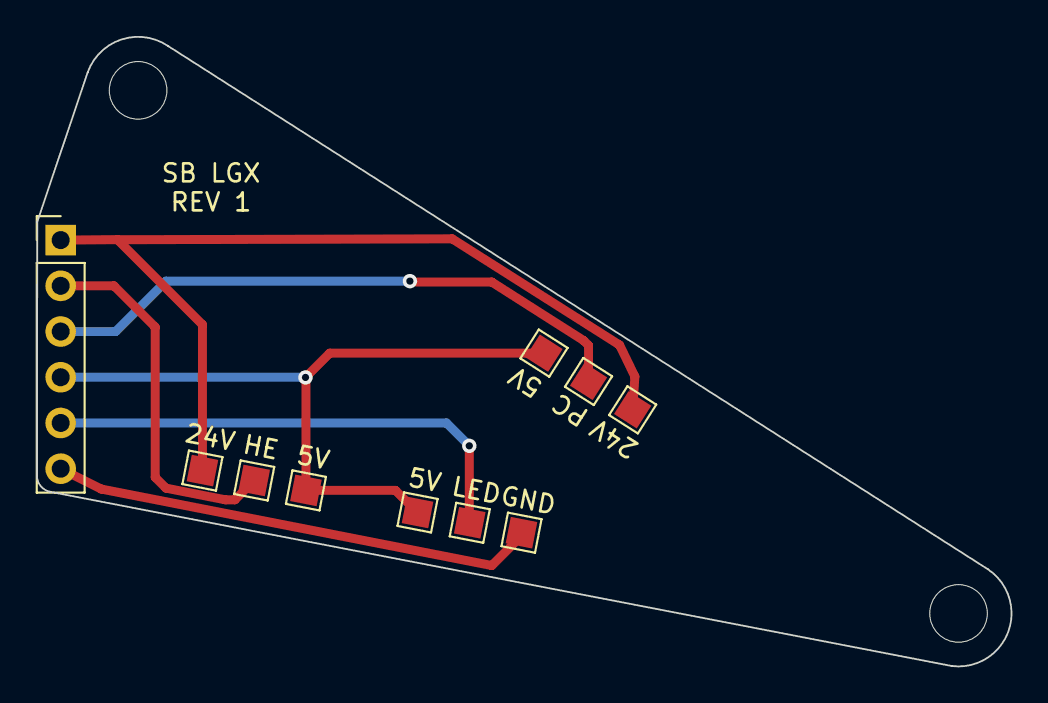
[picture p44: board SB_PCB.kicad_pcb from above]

Board: 2 copper layers, 54.1 x 35.0 mm, 12 parts (0 on the bottom side), 6 nets.

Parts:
5V: 5V PC Fan; TestPoint_Pad_1.5x1.5mm
5V#2: 5V HE Fan; TestPoint_Pad_1.5x1.5mm
5V#3: Solder Pad 5V; TestPoint_Pad_1.5x1.5mm
24V: 24V HE Fan; TestPoint_Pad_1.5x1.5mm
24V#2: 24V PC Fan; TestPoint_Pad_1.5x1.5mm
GND: Solder Pad GND; TestPoint_Pad_1.5x1.5mm
H1, H2: MountingHole; MountingHole_3.2mm_M3
HE: GND HE Fan; TestPoint_Pad_1.5x1.5mm
J1: Pin Header; PinHeader_1x06_P2.54mm_Vertical
LED: Solder Pad LED; TestPoint_Pad_1.5x1.5mm
PC: GND PC Fan; TestPoint_Pad_1.5x1.5mm

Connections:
5V: 5V.1, 5V#2.1, 5V#3.1, J1.4
24V: 24V.1, 24V#2.1, J1.1
GND: GND.1, J1.6
HE FAN: HE.1, J1.2
LED: J1.5, LED.1
PC FAN: J1.3, PC.1

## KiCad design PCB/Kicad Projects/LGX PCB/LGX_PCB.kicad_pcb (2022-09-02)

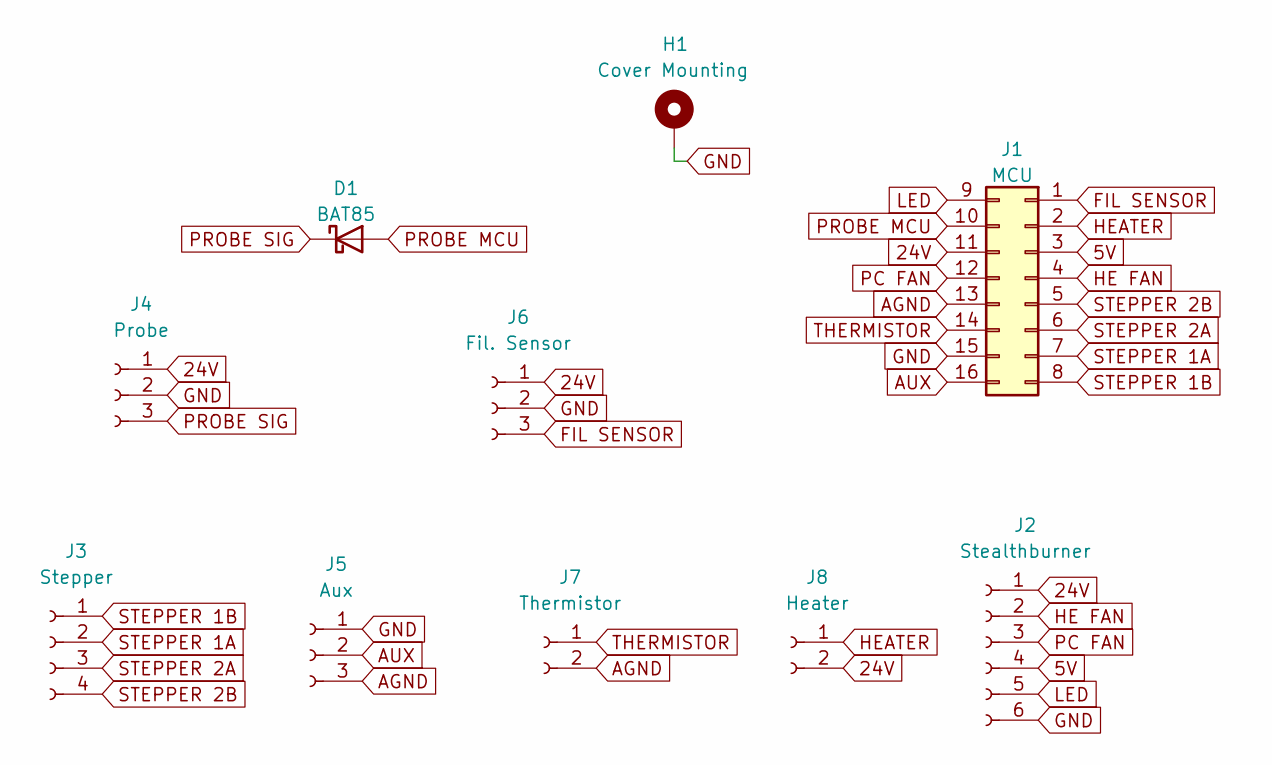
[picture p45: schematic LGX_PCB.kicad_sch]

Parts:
D1: BAT85; D_DO-35_SOD27_P7.62mm_Horizontal
H1: Cover Mounting; MountingHole_3.2mm_M3_Pad
J1: MCU; Molex_Micro-Fit_3.0_43045-1600
J2: Stealthburner; PinSocket_1x06_P2.54mm_Horizontal
J3: Stepper; JST_PH_B4B-PH-K_1x04_P2.00mm_Vertical
J4: Probe; JST_PH_B3B-PH-K_1x03_P2.00mm_Vertical
J5: Aux; JST_PH_B3B-PH-K_1x03_P2.00mm_Vertical
J6: Fil. Sensor; JST_PH_B3B-PH-K_1x03_P2.00mm_Vertical
J7: Thermistor; Molex_Micro-Fit_3.0_43650-0200
J8: Heater; Molex_Micro-Fit_3.0_43650-0200

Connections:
5V: J1.3, J2.4
24V: J1.11, J2.1, J4.1, J6.1, J8.2
AGND: J1.13, J5.3, J7.2
AUX: J1.16, J5.2
FIL SENSOR: J1.1, J6.3
GND: H1.1, J1.15, J2.6, J4.2, J5.1, J6.2
HE FAN: J1.4, J2.2
HEATER: J1.2, J8.1
LED: J1.9, J2.5
PC FAN: J1.12, J2.3
PROBE MCU: D1.2 (A), J1.10
PROBE SIG: D1.1 (K), J4.3
STEPPER 1A: J1.7, J3.2
STEPPER 1B: J1.8, J3.1
STEPPER 2A: J1.6, J3.3
STEPPER 2B: J1.5, J3.4
THERMISTOR: J1.14, J7.1

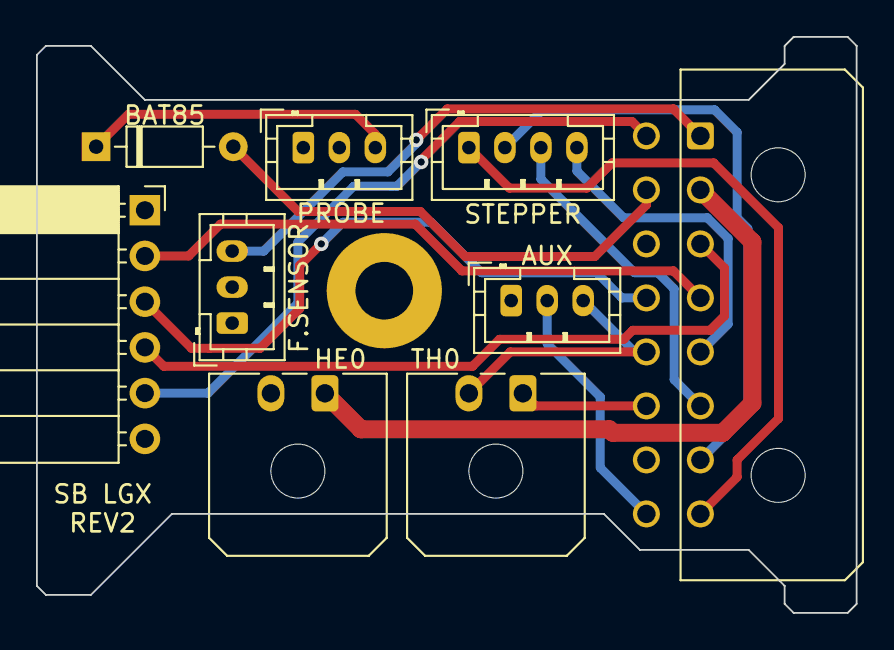
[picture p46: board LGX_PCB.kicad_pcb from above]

Board: 4 copper layers, 45.5 x 32.0 mm, 10 parts (0 on the bottom side), 17 nets.
